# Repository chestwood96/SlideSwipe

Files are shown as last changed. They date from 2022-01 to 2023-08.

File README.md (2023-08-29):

# SlideSwipe 1.0 (magnetic probe for the voron v0.1)
## Introduction
I liked the idea of the [SideSwipe](https://github.com/oldfar-t/Side-Swipe-Magnetic-Probe) probe but didn't like that it would require either printing with the door open or losing Y travel, so I made my own take on the idea.

Taking probe             |  Stowing probe
:-------------------------:|:-------------------------:
Take  |  Stow

## Pros and cons compared to SideSwipe
| Pro | Con |
| ---- | ---- |
| + Fully integrated | - Requires new cowling (and the accompanying rebuild of everything on it) |
| + Cables well hidden | - More complex (more parts, more steps) |
| + No loss in y area with the door closed |  |
| + Bed can't hit the arm |  |
| + Hot-swappable switches (ok, fair that's a bit of a gimmick)

There is also the [option](Alternative_Mounts/FrontCowlingMount/README.md) of mounting it to the front of the cowling instead of using a new cowling if that is not an option.

## BOM
### Parts
- 1x MG90s Metal gear servo (the SG90 plastic gear ones work too but are not reccomended)
- 1x Omron(or omron size) mouse switch (I am using a kailh GM4.0 switch, but it's only marginally better than all the other switches I tested)
- 5x 6x3mm round magnets (I used the cheapest crappiest ones I could find off aliexpress, need to be at least 2.7mm thick)
- 1x 300mm servo extender cable (or make your own)
- 1x 1.5m of stranded wire with <1.2mm od (I tested 30awg silicone wire and 26awg ptfe wire)
- 2x JST-XH housing (only one housing and 2 crimping terminals if you don't want to wire to the 5pin probe port on the SKR mini E3 v2)
- 7x JST-XH female crimping terminal
- 1x (optional but reccomended) JST-PH or JST-XH 2pin male and female connector pair
- 3x 16mm piece of 4od2id PTFE tube (does not need to be the nice stuff)
- 1x 7mm piece of 4od2id PTFE tube (does not need to be the nice stuff) 
### Screws
- 7x M3x6 Socket head screw (cap head probably work too, as long as they are at least slightly attracted to magnets)
- 2x M3x8 Cap head screw
- 2x M3 nut
### Tools
- Some superglue
- Tools to crimp JST-XH (and optionally JST-PH)
- A multimeter

## Printing
All parts are designed to print in the orientation they come in and do not require supports (If you have really bad overhang performance you can add a bit of support for the probe but it should not be necessary).

Designed to print in ABS at 0.4mm outer perimeter width and 0.2mm layer height.

I recommend ironing for the following parts, the rest can be printed without:
- Arm1
- Arm2
- ProbeCarrierTop
- ProbeCarrierBottom
- RailMountTop

If you are going to do accents, I recommend printing the following parts in the accent color:
- Arm1
- Arm2
- Probe

## Build
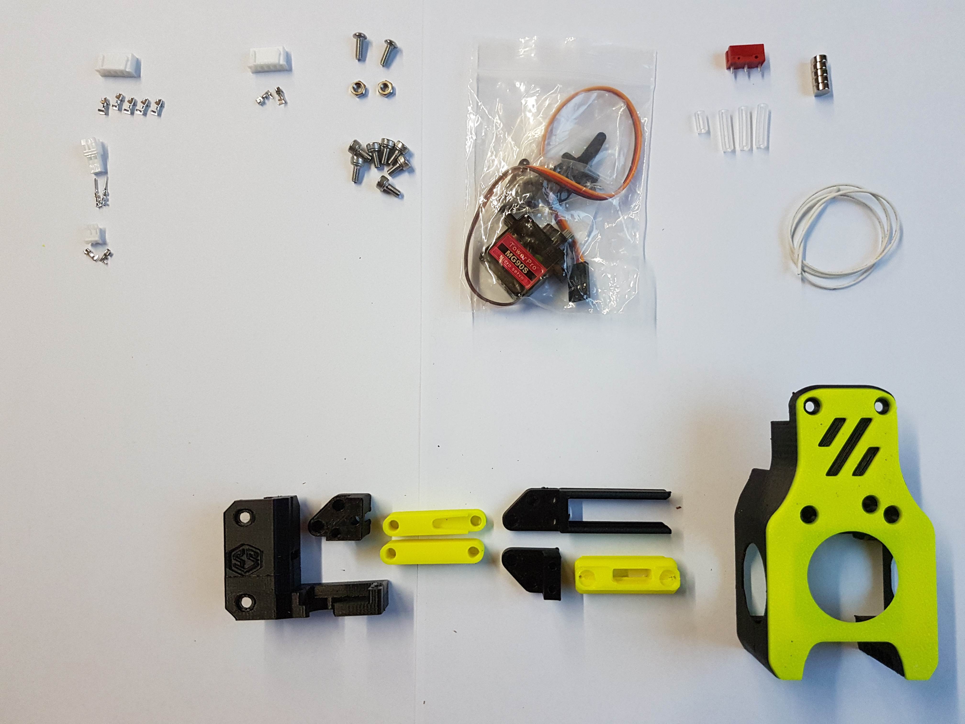
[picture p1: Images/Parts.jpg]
Parts

### Probe
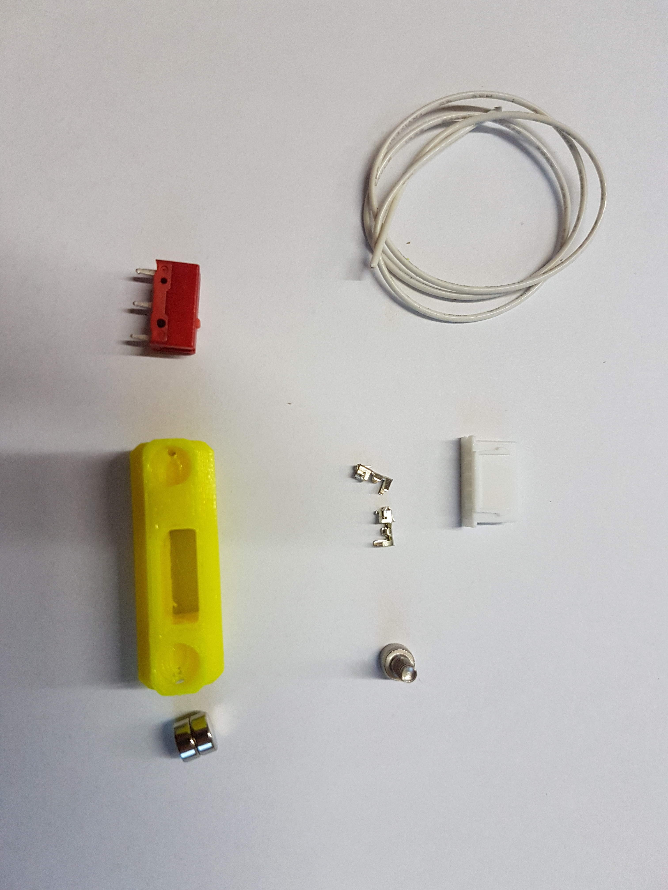
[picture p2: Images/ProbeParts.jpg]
ProbeParts


Crimp two short (about 5cm but cutting off is easier than adding...) pieces of wire and put them in the outer-most places in the JST-XH 5pin housings. I recommend testing the cripms at this point.
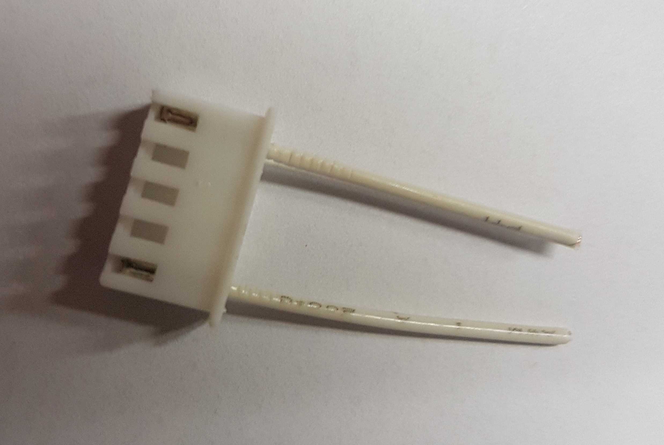
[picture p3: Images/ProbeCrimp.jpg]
ProbeCrimp


Thread the wires through the holes, then put the connector in the probe. Make sure it's the right way around. Don't put it in all the way yet.
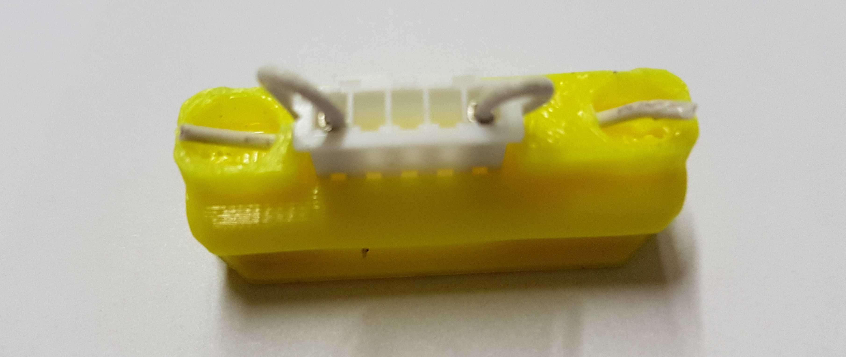
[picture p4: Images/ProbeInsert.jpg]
ProbeInsert


Add some superglue to the back of the connector and carefully push it all the way in while making sure the wires are not pinched. Make sure superglue does not get anywhere it shouldn't.
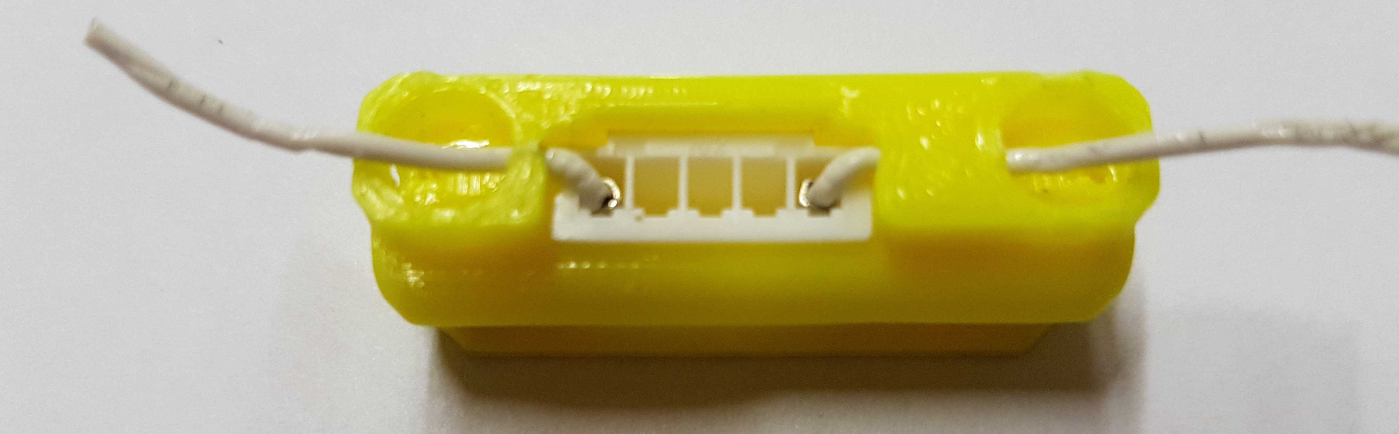
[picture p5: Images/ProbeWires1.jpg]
ProbeWires1


Shorten the wires, so they extend a little past the edge (5-10mm is fine).
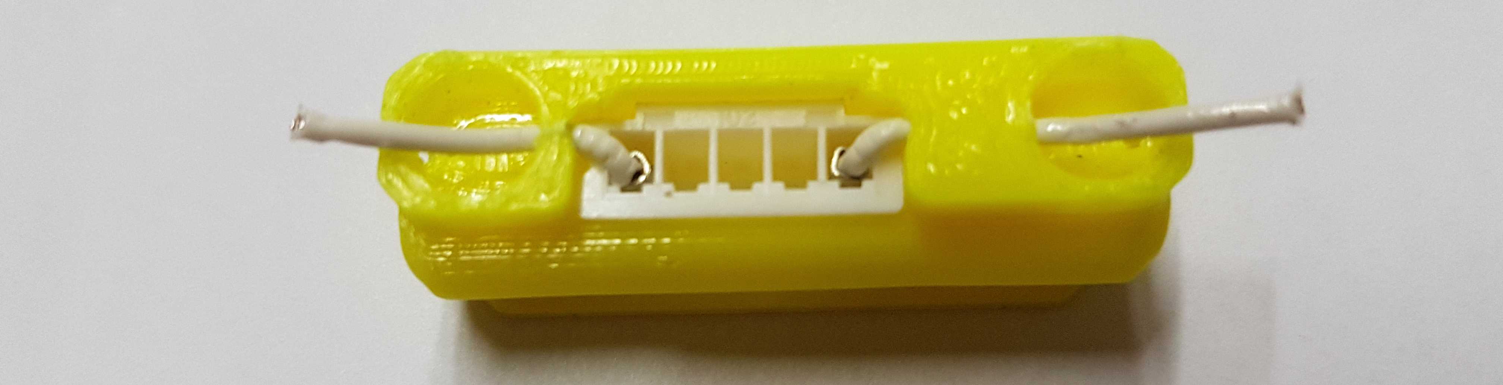
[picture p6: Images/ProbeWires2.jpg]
ProbeWires2


Strip as much of the wire as you can. You probably can't use normal wire strippers for that.
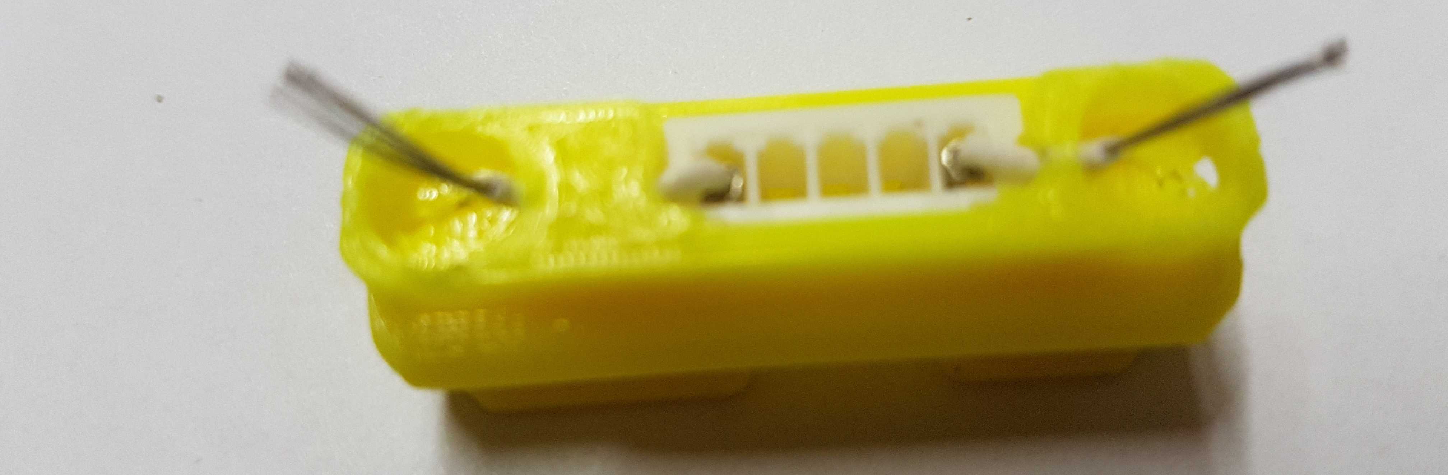
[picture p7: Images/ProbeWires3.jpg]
ProbeWires3


Put the stripped wires in the magnet holes. Make sure the unstripped parts are in the grooves, so they don't get in the way.
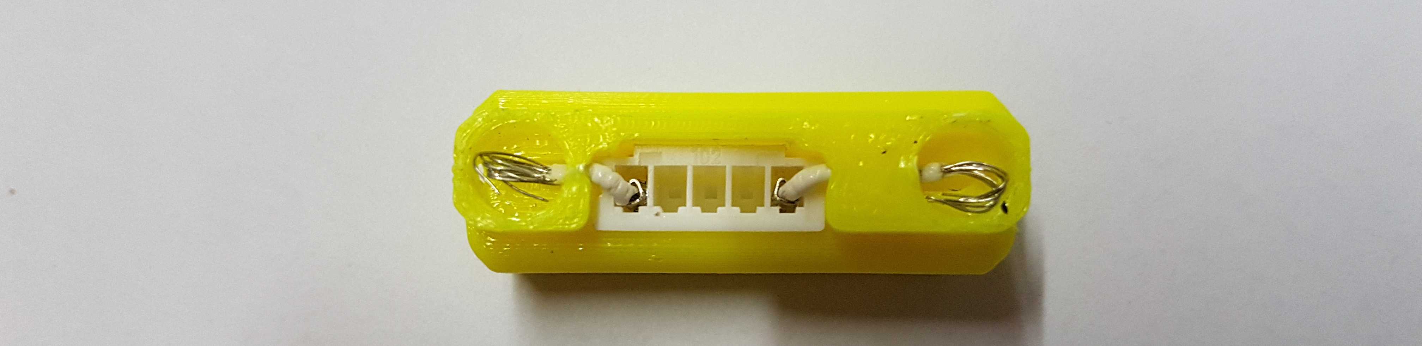
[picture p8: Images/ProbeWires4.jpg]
ProbeWires4


Add some superglue to the rim of the holes and put the magnets in the holes **with the same polarity facing up**. Make sure the glue does not get on the wires too much and there is none on the top of the magnets. Also, try to get them as parallel with each other as possible (pressing them against a flat surface while drying helps). 

Test continuity between the magnet and the jst pins.
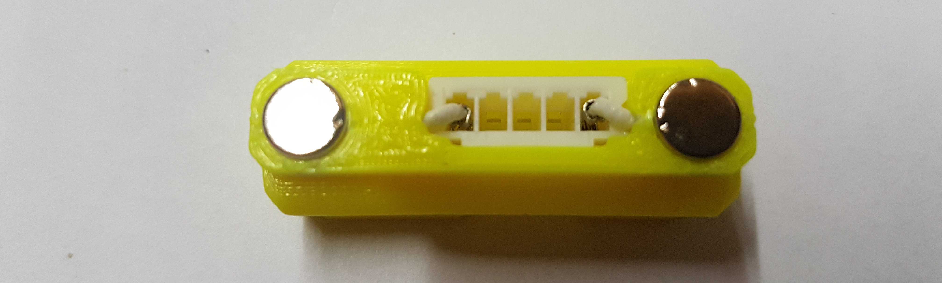
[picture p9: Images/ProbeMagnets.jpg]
ProbeMagnets


After the glue has dried insert the microswitch so the plunger is in the middle of the probe.

With the switch inserted there should be continuity between the magnets unless the switch is pressed.
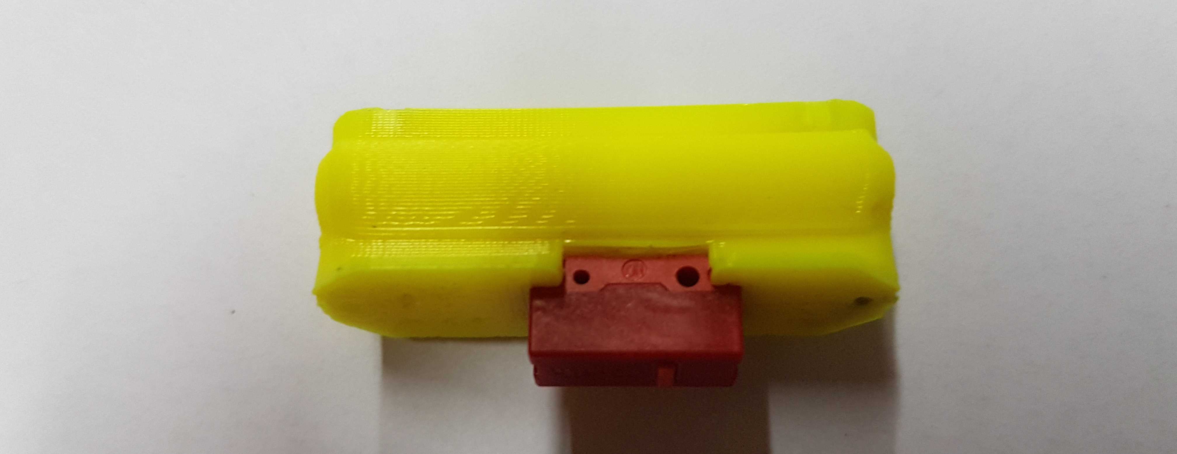
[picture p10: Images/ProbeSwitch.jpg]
ProbeSwitch


Screw on an M3x6 screw into the hole of the side of the probe. (Make sure the screw is at least somewhat attracted to a magnet)
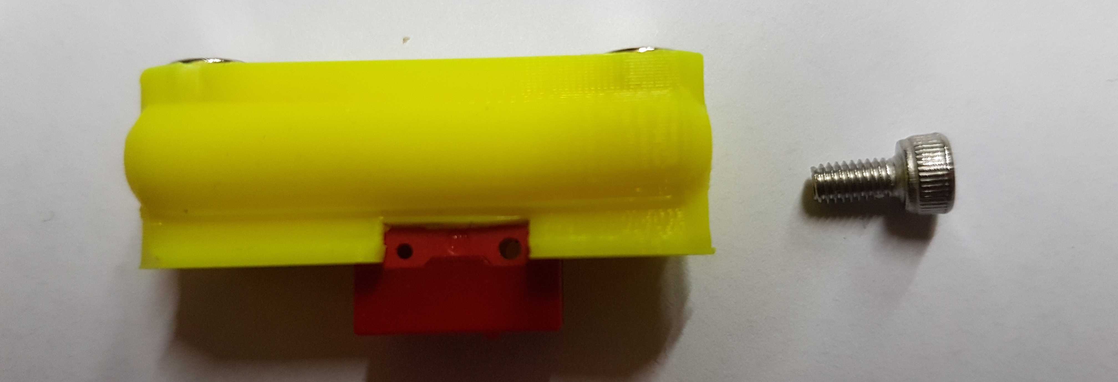
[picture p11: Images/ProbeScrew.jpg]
ProbeScrew

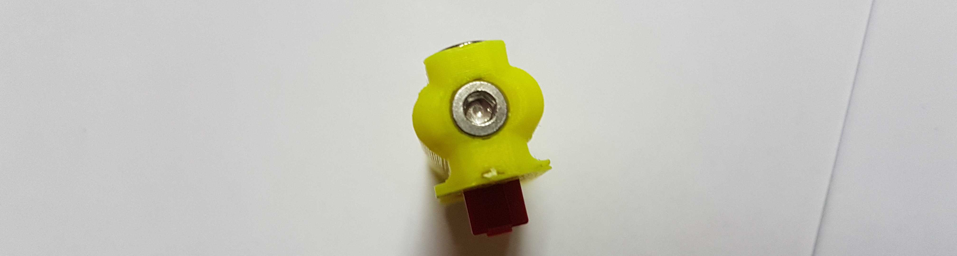
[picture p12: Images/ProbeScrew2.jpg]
ProbeScrew2


The screw is not only attracted to magnets in one direction (because of the influence from the magnet above it). Install the retention magnet in the probe carrier in the right orientation (using the probe as a tool for installing it can help). Then add some glue to the back of the magnet to hold it in place (there is a hole in the part to allow easier gluing and removal of the magnet)
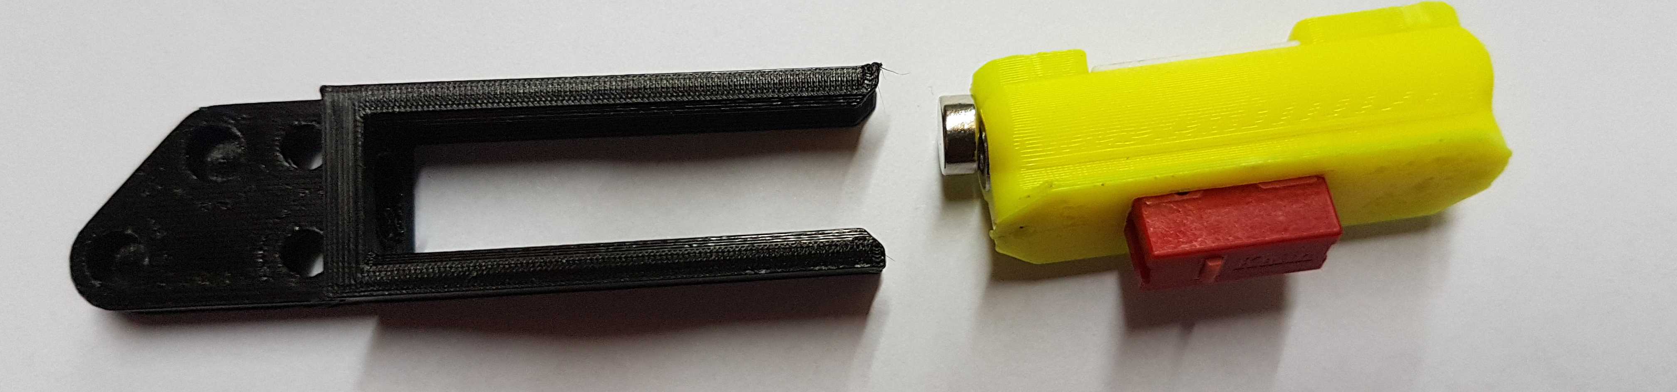
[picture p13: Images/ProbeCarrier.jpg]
ProbeCarrier

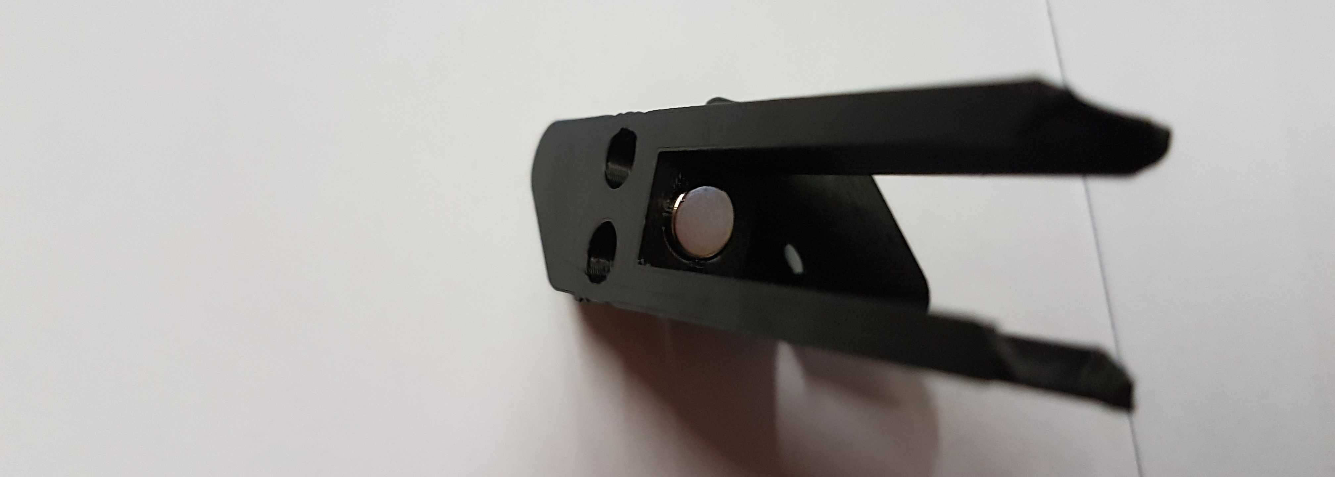
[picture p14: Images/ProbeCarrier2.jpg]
ProbeCarrier2


The probe should now stick in the carrier and not just fall out.
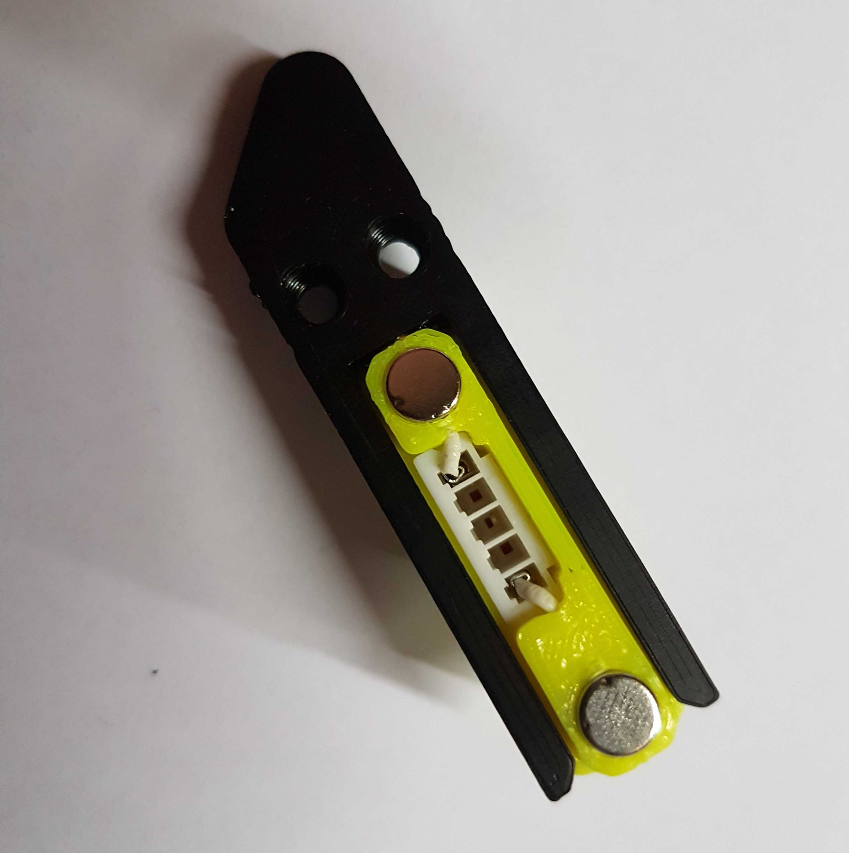
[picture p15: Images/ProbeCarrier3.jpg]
ProbeCarrier3


### Cowling
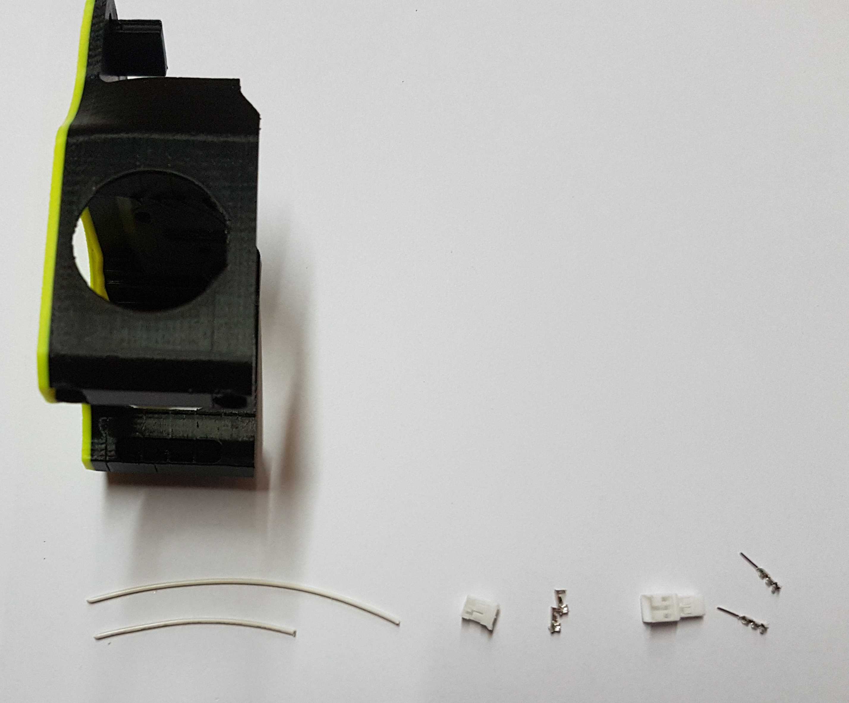
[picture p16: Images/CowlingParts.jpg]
CowlingParts


In this guide I am putting a connector (jst-ph) on the cowling for easier removal, you can use any other small enough connector or wire it directly (you just need to make the wires long enough to go through the umbilical and to your mainboard plus a little slack, so you can take the cowling of at least somewhat)

Crimp your connector to two short pieces of wire to your connector and feed them through the wire holes in the back of the cowling. Check your crimps.
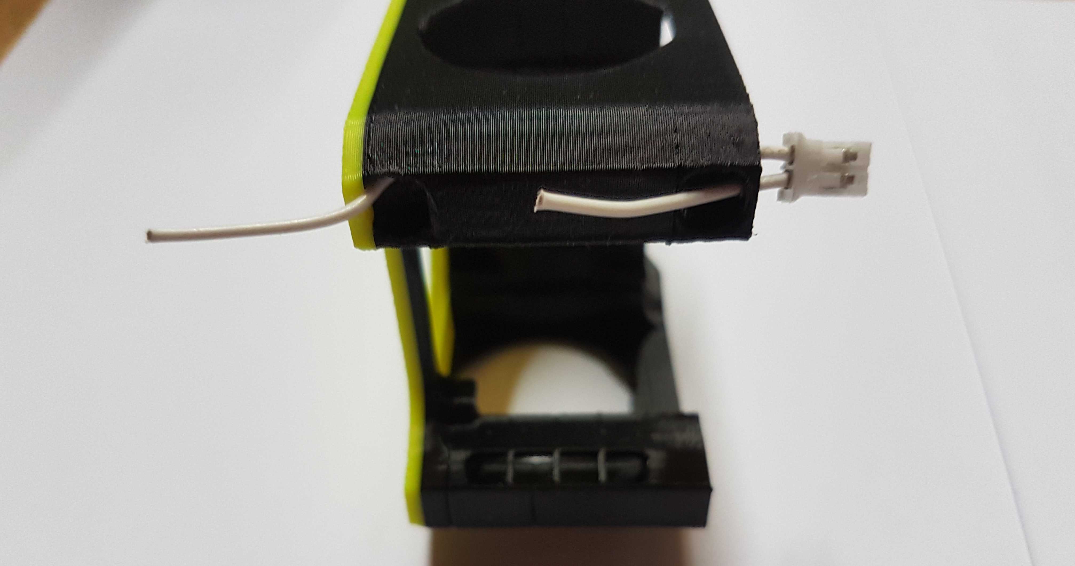
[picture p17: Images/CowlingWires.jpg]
CowlingWires


Cut them so about 3-4cm of wire are extending past the holes, then strip about 2cm off those.
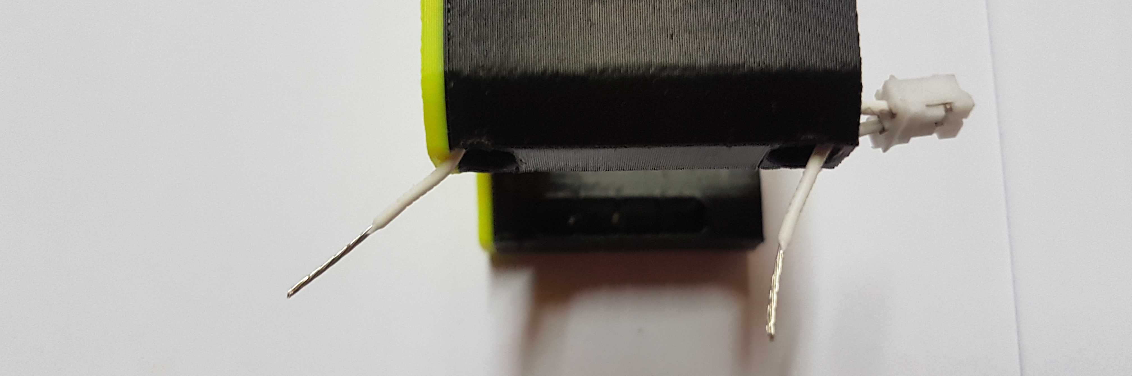
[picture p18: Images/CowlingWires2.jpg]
CowlingWires2


Pull the wires back until there is only stripped wire in the holes and curl the rest of the wire in the holes.
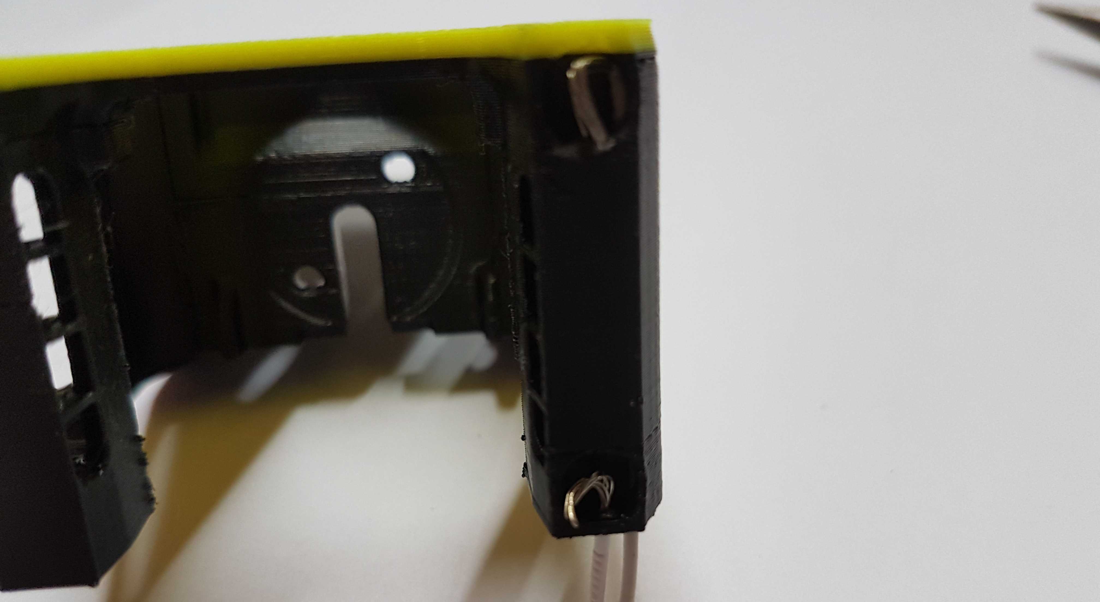
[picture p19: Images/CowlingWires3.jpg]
CowlingWires3


Put some superglue on the rims of the holes and push the magnets in the holes **in the right orientation to match the probe**. Try to get those two as parallel to each other as possible by pushing them against a flat surface.

Make sure there is no glue on the top of the magnets and check continuity between the magnets and the wires.

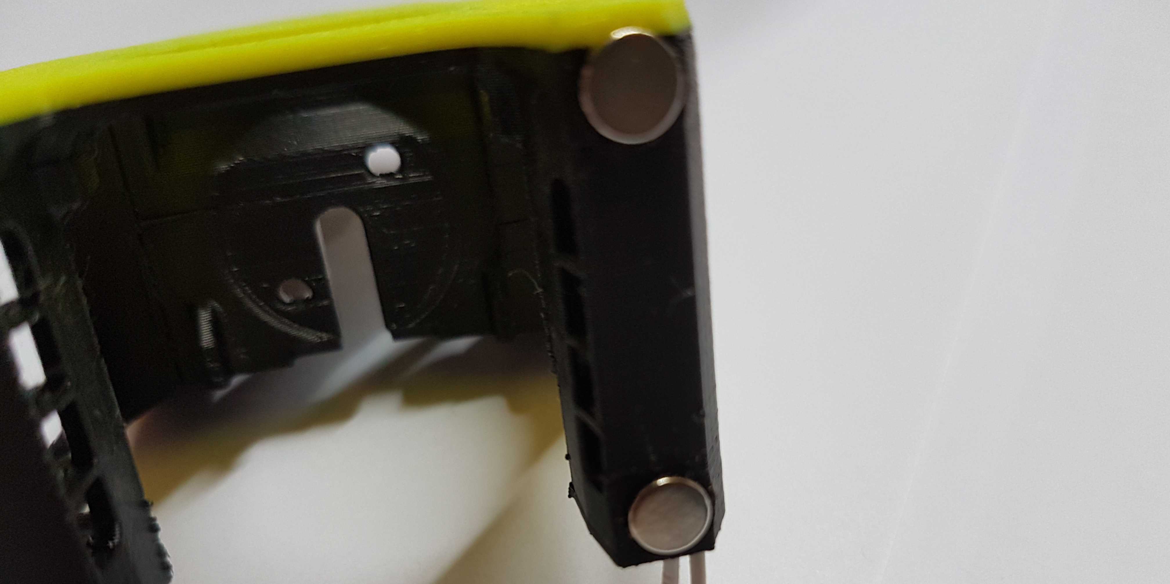
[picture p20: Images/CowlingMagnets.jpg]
CowlingMagnets


If the magnets were put in the right way the probe should stick to the cowling. Test the continuity between the wires. There should be continuity between the wires unless the switch is pressed or the probe is removed.
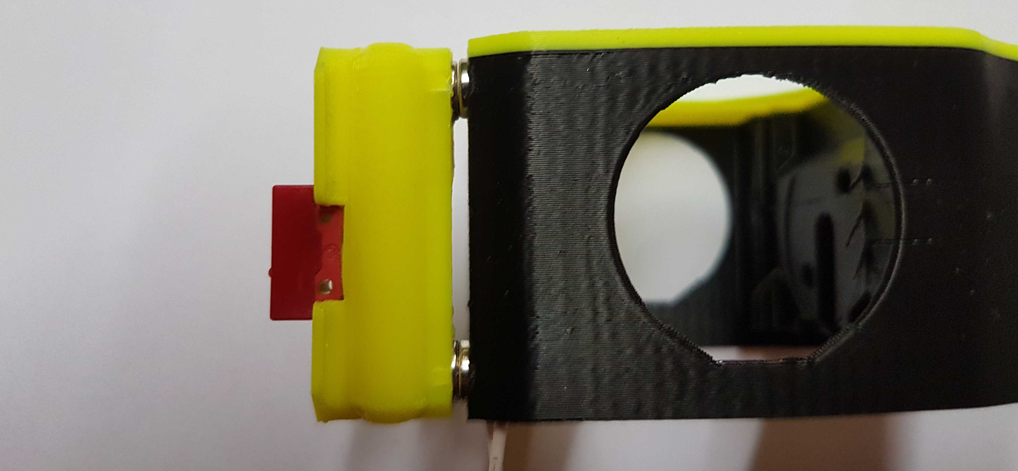
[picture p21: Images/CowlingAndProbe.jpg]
CowlingAndProbe


### Probe holder
Find the servo arm that fits the arm the best and cut off anything else on that arm if there is anything.
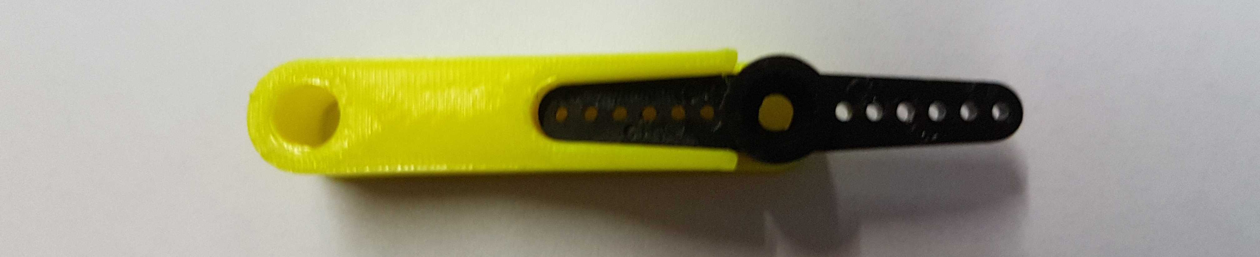
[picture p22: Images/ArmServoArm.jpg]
ArmServoArm

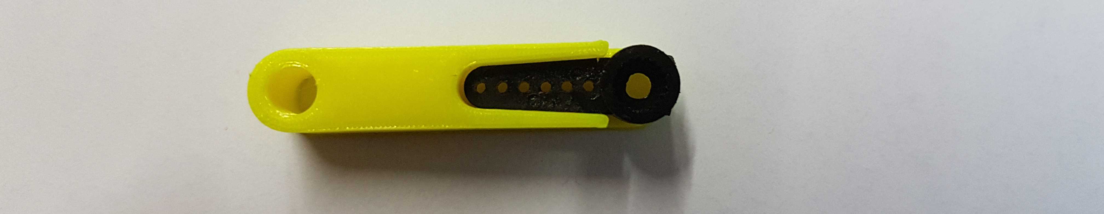
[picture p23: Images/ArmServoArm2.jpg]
ArmServoArm2


Zero the servo (and check that it has at least over 90° of travel and isn't a continuously rotating one) and install the chosen arm so it points a little over 90° when at the max point (picture is the max point).
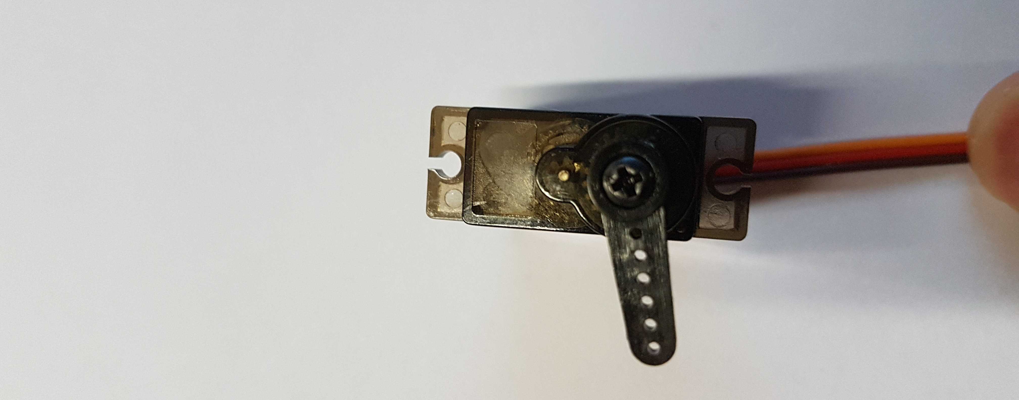
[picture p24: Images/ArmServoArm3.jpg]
ArmServoArm3


Pull the servo wire through the hole.
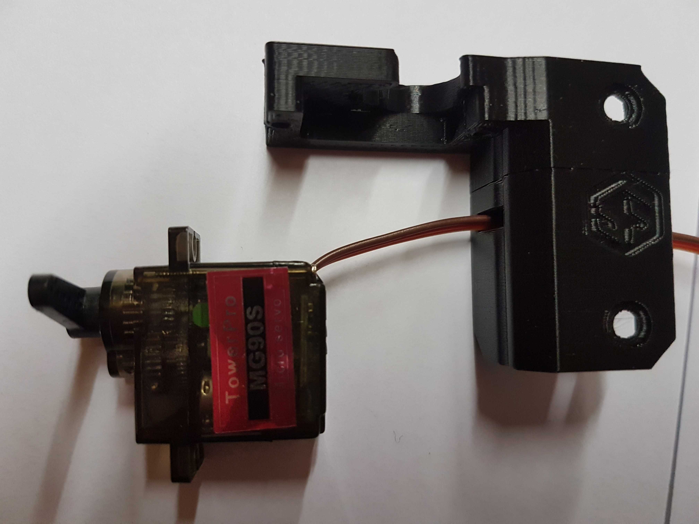
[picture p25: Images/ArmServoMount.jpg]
ArmServoMount


Insert the servo into the mount and fix it using 2 M3x6 screws
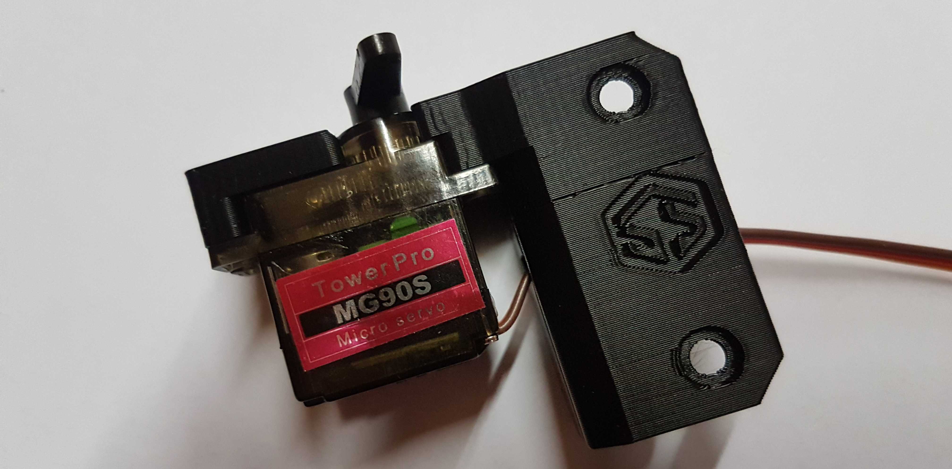
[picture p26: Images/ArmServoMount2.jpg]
ArmServoMount2

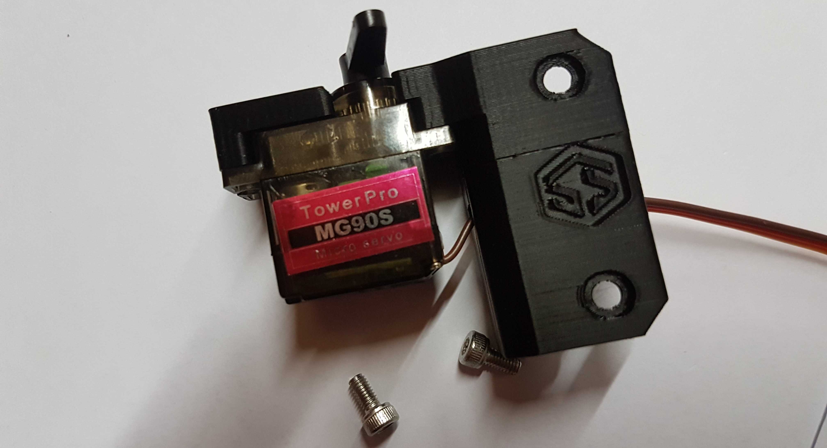
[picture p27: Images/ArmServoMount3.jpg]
ArmServoMount3

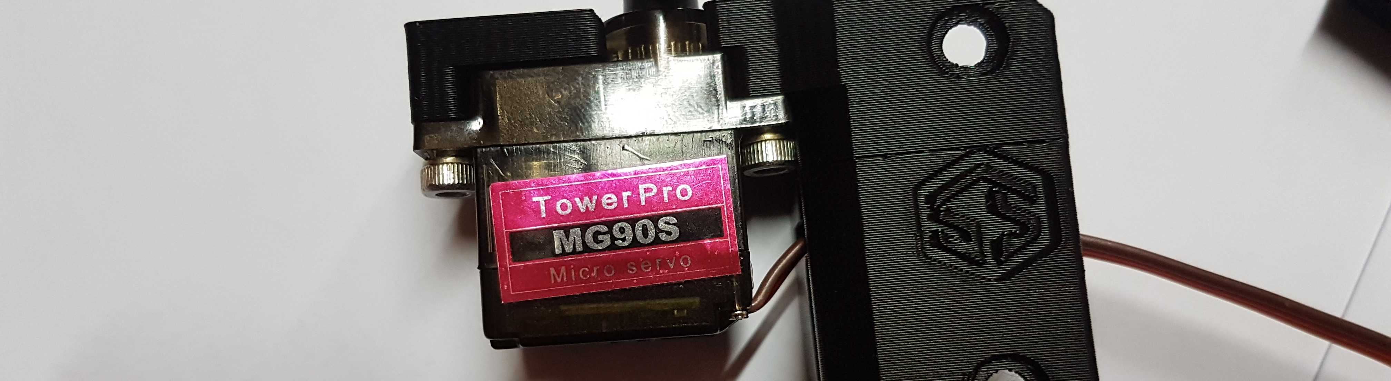
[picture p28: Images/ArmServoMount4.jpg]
ArmServoMount4


Insert the short piece of PTFE in the left hole of "RailMountTop".
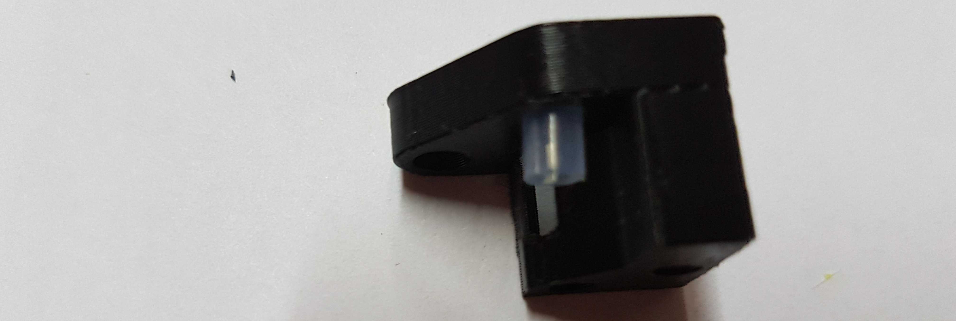
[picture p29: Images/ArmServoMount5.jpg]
ArmServoMount5


Insert one of the longer pieces of ptfe into one of the holes of "Arm2" (the solid one).
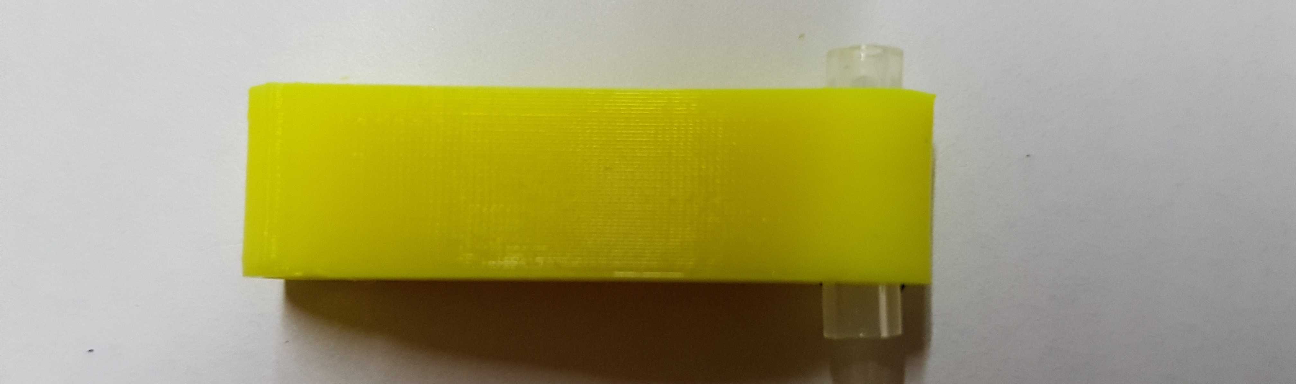
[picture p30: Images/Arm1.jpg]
Arm1


Put "Arm2" and "Arm1" onto the servo carrier like shown.
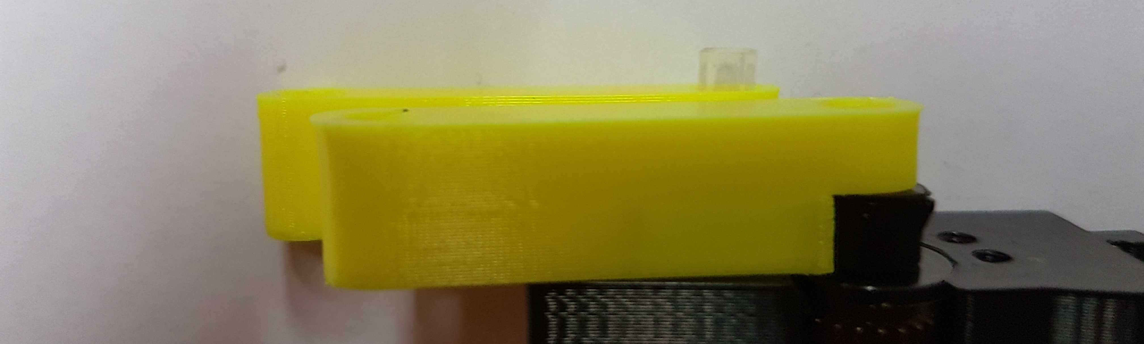
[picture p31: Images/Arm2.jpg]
Arm2


Screw "RailMountTop" onto the servo carrier using 2 M3x6 screws.
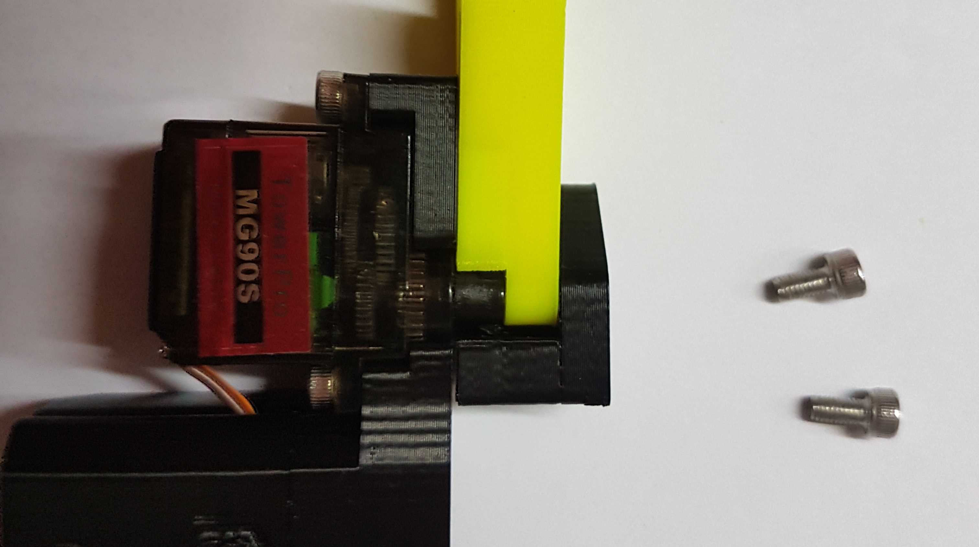
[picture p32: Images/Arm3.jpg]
Arm3


Put the other two longer pieces of ptfe into the remaining two holes in the arms.
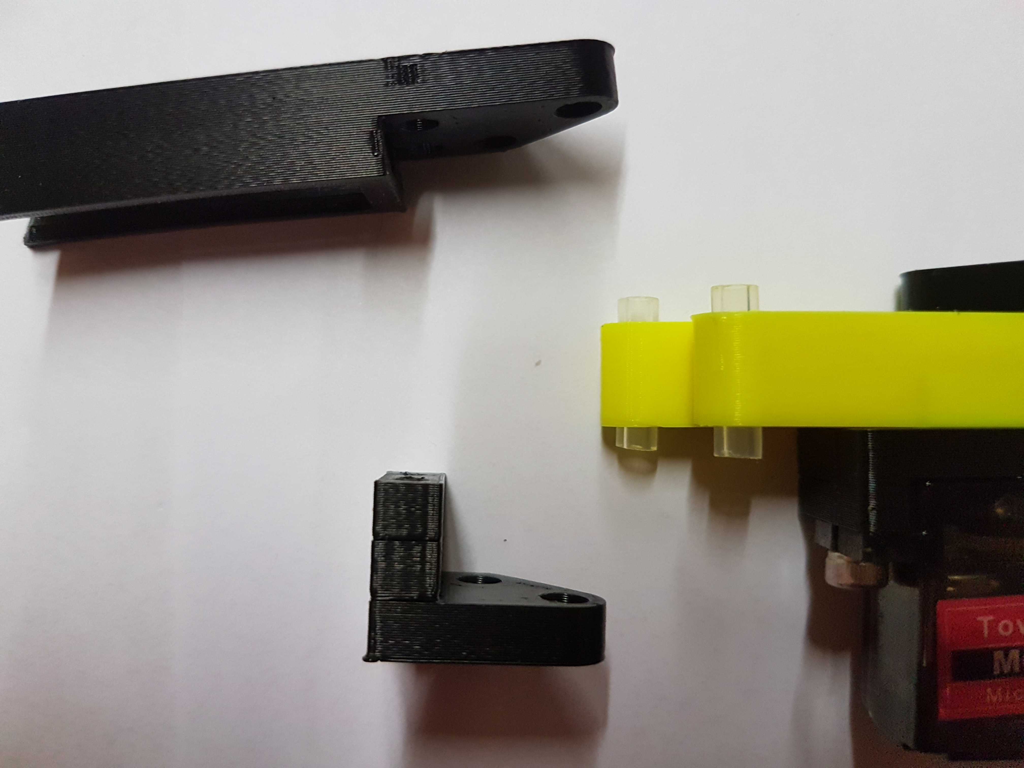
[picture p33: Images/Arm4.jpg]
Arm4


Put "ProbeCarrierTop" and "ProbeCarrierBottom" on the arms and screw them down using 2 M3x6 screws.
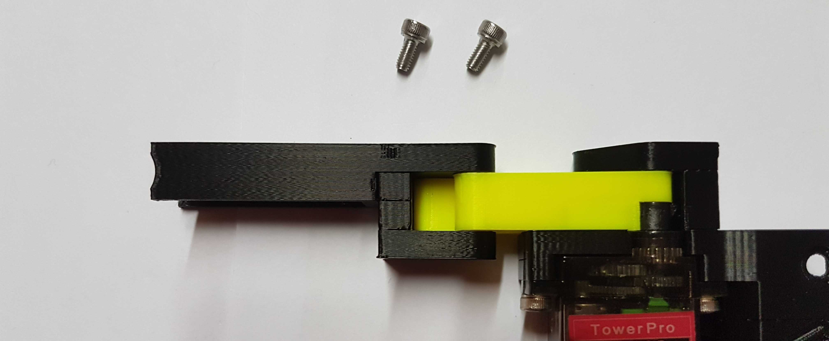
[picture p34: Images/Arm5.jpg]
Arm5

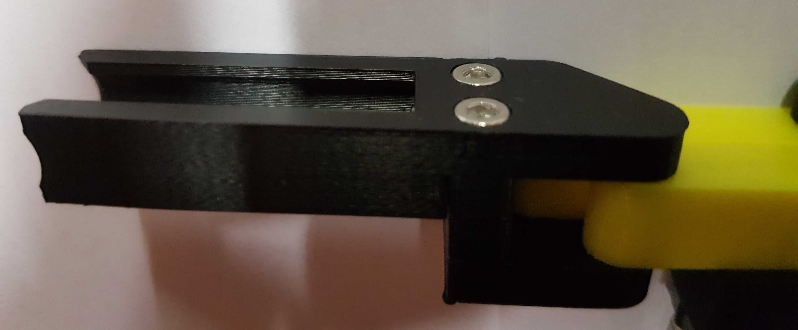
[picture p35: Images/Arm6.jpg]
Arm6


Add nuts in the pockets on the inside of the mount.
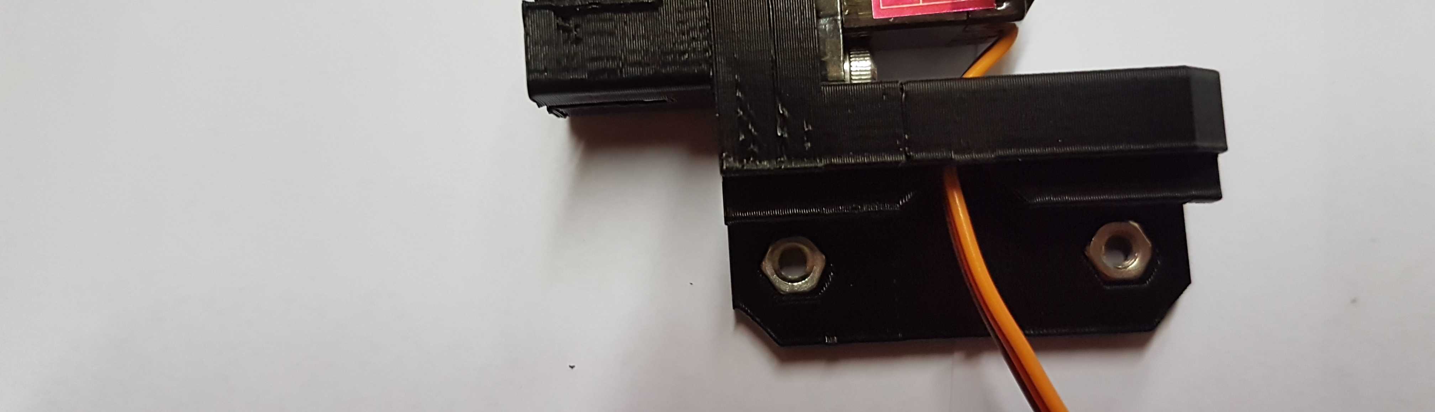
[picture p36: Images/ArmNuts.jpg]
ArmNuts


That should be the physical build done.
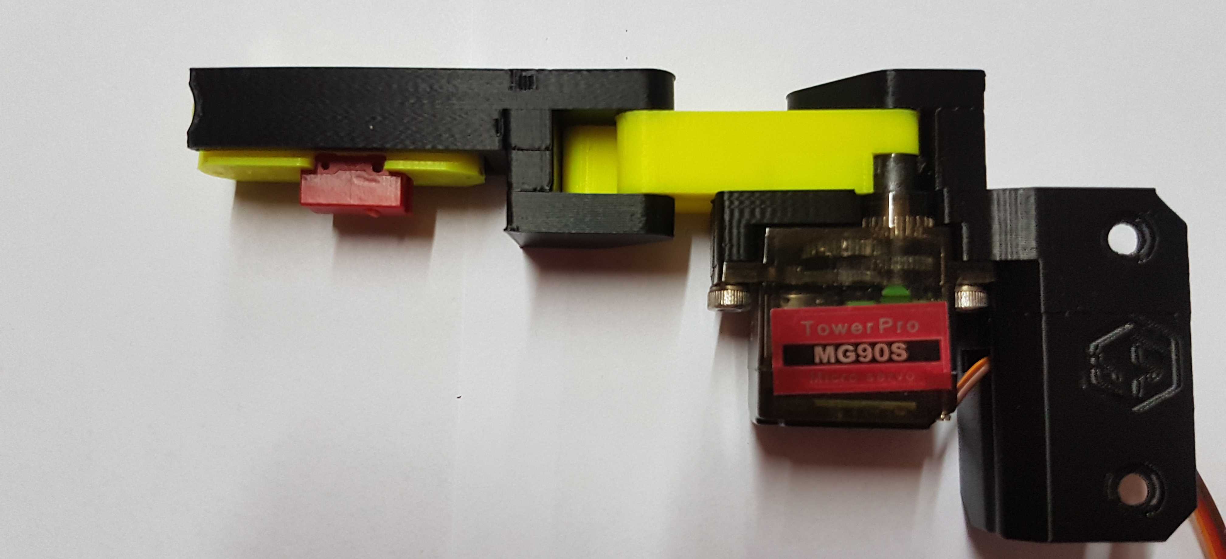
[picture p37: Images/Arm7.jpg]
Arm7


## Installation
### Installing the new cowling
The installation is the same as with the regular one, refer to the manual for that.

### Installing the probe arm
put the servo wire into the groove of the extrusion and tip the mount into it. Fix the assembly using the screws on the side.

Adjust the height to where it can grab the probe, but the arm does not hit the printhead then fix it in place.

Route the servo wire through the slot in the front extrusion upwards into the slot of the top extrusion. The stock wire should be just long enough to pass through the panel, though you'll probably have to remove the connector housing for that.

## Wiring
In this example I am hooking up to the "BL-Touch" connector of the SKR mini e3 v2.0

If you are fancy you can crimp that onto a 5 pin jst-xh plug, otherwise you can just plug it straight into the header.

Here is a crude diagram of how this could be wired up. If you wired it differently you'll need to pay special attention during the klipper setup.
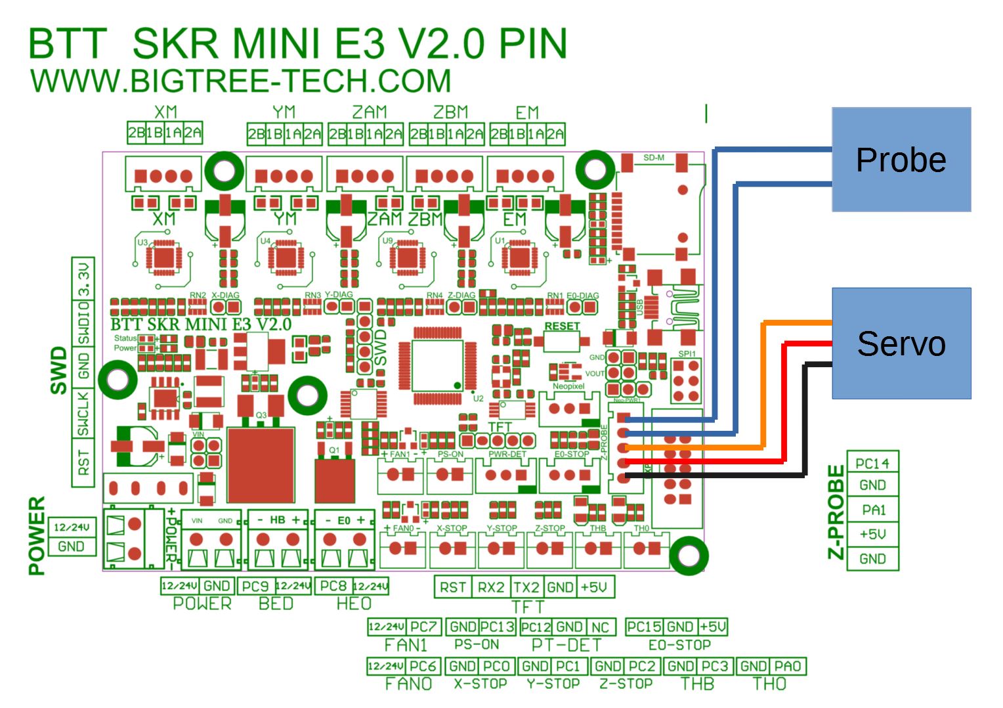
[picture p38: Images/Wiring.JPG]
Wiring


## Klipper setup

Put this in your klipper config. If you wired it differently, adjust the pins for the probe and the servo
```
[homing_override]
axes: z
gcode:
    SET_KINEMATIC_POSITION Z=0
    G1 Z5
    G28 X Y
    Query_Probe
    SS_CONDITIONAL_TAKE_PROBE
    G1 X40 Y110
    G28 Z
    G91
    G1 Z1
    G90

[probe]
pin: ^PC14
x_offset: 20
y_offset: 0
z_offset: 10
speed: 20.0
samples: 2
sample_retract_dist: 5.0
lift_speed: 30.0
samples_tolerance: 0.01
samples_tolerance_retries: 15
deactivate_on_each_sample: 0

[bed_mesh]
speed: 200
horizontal_move_z: 25
mesh_min: 25,25
mesh_max: 95, 95
probe_count: 3,3
algorithm: bicubic

[servo probeServo]
pin: PA1
minimum_pulse_width: 0.000544

[gcode_macro SS_PICKUP_POS]
variable_x: 115
variable_y: 50
variable_z: 30
gcode:
  M118 pickup pos X:{printer["gcode_macro SS_PICKUP_POS"].x} Y:{printer["gcode_macro SS_PICKUP_POS"].y} Z:{printer["gcode_macro SS_PICKUP_POS"].z}

[gcode_macro SS_DEPLOY]
gcode:
    SET_SERVO SERVO=probeServo ANGLE=160
    G4 P500 # wait for deploy
    #SET_SERVO SERVO=probeServo WIDTH=0 # OFF
    
[gcode_macro SS_RETRACT]
gcode:
    SET_SERVO SERVO=probeServo ANGLE=20
    G4 P500 # wait for retract
    SET_SERVO SERVO=probeServo WIDTH=0 # OFF

[gcode_macro SS_TAKE_PROBE]
gcode:
    G1 Z{printer["gcode_macro SS_PICKUP_POS"].z} F5000
    G1 X{printer["gcode_macro SS_PICKUP_POS"].x - 20} Y{printer["gcode_macro SS_PICKUP_POS"].y} F5000
    SS_DEPLOY
    G1 X{printer["gcode_macro SS_PICKUP_POS"].x}
    G1 Y{printer["gcode_macro SS_PICKUP_POS"].y + 50}
    G1 X{printer["gcode_macro SS_PICKUP_POS"].x - 20}
    SS_RETRACT

[gcode_macro SS_STOW_PROBE]
gcode:
    G1 Z{printer["gcode_macro SS_PICKUP_POS"].z} F5000
    G1 X{printer["gcode_macro SS_PICKUP_POS"].x - 20} Y{printer["gcode_macro SS_PICKUP_POS"].y + 50} F5000
    SS_DEPLOY
    G1 X{printer["gcode_macro SS_PICKUP_POS"].x}
    G1 Y{printer["gcode_macro SS_PICKUP_POS"].y} F2000
    G1 X{printer["gcode_macro SS_PICKUP_POS"].x - 20} F5000
    SS_RETRACT

[gcode_macro SS_CONDITIONAL_TAKE_PROBE]
gcode:
    {% set P = printer.probe.last_query %}
    {% if P %}
        SS_TAKE_PROBE
    {% endif %}

[gcode_macro SS_CONDITIONAL_STOW_PROBE]
gcode:
    {% set P = printer.probe.last_query %}
    {% if not P %}
        SS_STOW_PROBE
    {% endif %}

[gcode_macro G29]
gcode:
    G91
    G1 Z1
    G90
    Query_Probe
    SS_CONDITIONAL_TAKE_PROBE
    BED_MESH_CALIBRATE
    SS_STOW_PROBE

[force_move]
enable_force_move: True

[respond]
```

and replace your z endstop with the probe:
```
endstop_pin: probe:z_virtual_endstop
```

Also add the following to your print start (either in klipper or in your slicer) to make sure it won't try to print with the probe attached (the query_probe first is important):
```
    Query_Probe
    SS_CONDITIONAL_STOW_PROBE
```

After the calibration you should be able to use the G29 macro to mesh level your bed.

### Calibrating the servo angles
Using the servo command, find good values where the servo reliably hits the deployed and stowed position. The mechanism mechanically limits the travel. Having the servo try to push against it the whole time isn't great for it, so try to find some values that don't go way over the limits.

Once you have found the right values, update the "SS_DEPLOY" and "SS_RETRACT" macros with your new values.

### Calibrating the pickup position
This should already be somewhat acurate but if it isn't find the pickup position and update the "SS_PICKUP_POS" macro accordingly.

## First tests
### Check the probe and config
Let's see if klipper can see the probe. The "QUERY_PROBE" command is our friend here.

With the probe attached (by hand for now) it should return "open". With the button pressed it should return "triggered" and with the probe removed it should also return "triggered". If this is not true don't proceed, and go check your wiring and config.

If that worked out put the probe in the probe carrier and do a test run. The homing override uses the probe so all we'll have to do to see if it works is run `G28`.

It should now home x and y, then pick up the probe and probe for Z. Be ready to cut power if something weird happens.

To make sure everything has settled I like to do a couple hundred probes before I do stuff like calibrating the Z-offset.

```
PROBE_ACCURACY samples=100
```

## Calibrate Z-Offset and start printing
Use your favourite method of calibrating the z-offet and start printing.

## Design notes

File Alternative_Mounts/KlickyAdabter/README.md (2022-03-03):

# Front Cowling Mount
Thanks to Jlas1 for making this.

This is an adapter that allows using SlideSwipe on cowlings meant for klicky like the regular klicky cowling or the one for the LGX Lite.

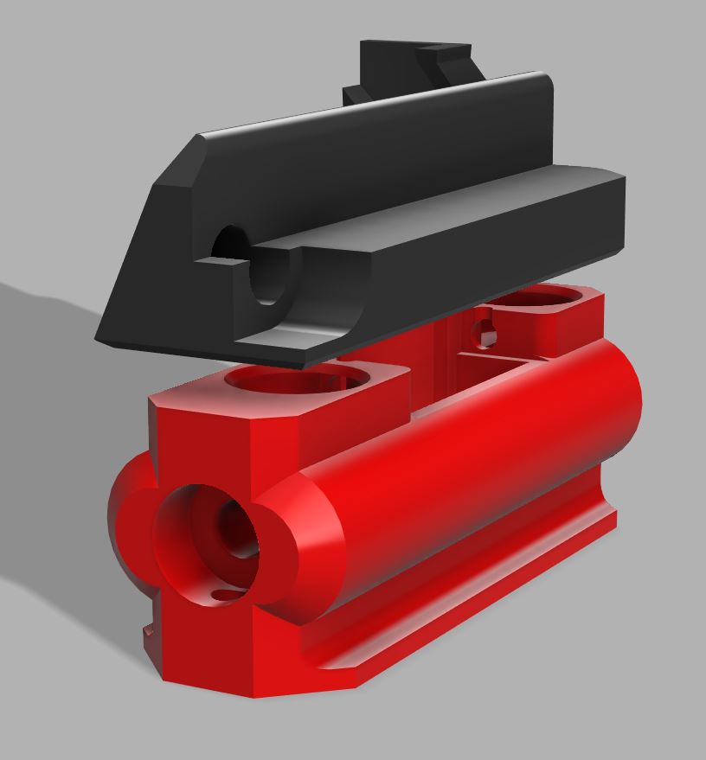
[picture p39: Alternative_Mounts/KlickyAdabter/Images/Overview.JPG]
Action


## Pros and cons compared to integrated mount
| Pro | Con |
| ---- | ---- |
| + Allows keeping the same Cowling (if you allready use one of the compatible ones) | - Probe is further away from the nozzle (can probe less of the bed) |
| + Allows switching between Klicky and Slideswipe | - Uses a slightly different probe that is not compatible with the other mounting options |

## BOM (Differences only)
### Screws
- 1x M3x6 BHSC screw

## Build
The build process is the same as normal, just substitute the cowling with the "Slideswipe_KlickyAdapter_mount" and the probe with "Slideswipe_KlickyAdapter_probe"

## Klipper Setup
The klipper setup is also almost the same, however we need a few changes, **do not try probing before this step**

## Pickup position
Move the X of the pickup position 8mm to the left, to do this change this part of the "SS_PICKUP_POS" macro from:
```
[gcode_macro SS_PICKUP_POS]
variable_x: 115
...
```
to:
```
[gcode_macro SS_PICKUP_POS]
variable_x: 107
...
```

## Probe offset
Increase the X-offset of the probe by 8mm (to 28mm):
```
[probe]
pin: ^PC14
x_offset: 28
...
```

## Change Mesh Leveling coordinates
Replace the whole "[bed_mesh]" section with this:
```
[bed_mesh]
speed: 200
horizontal_move_z: 25
mesh_min: 32,32
mesh_max: 88, 88
probe_count: 3,3
algorithm: bicubic
```

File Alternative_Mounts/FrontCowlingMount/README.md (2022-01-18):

# Front Cowling Mount
Thanks to Jlas1 for making this.

The Front cowling mount allows using SlideSwipe without printing and installing a new cowling.

Action

## Pros and cons compared to integrated mount
| Pro | Con |
| ---- | ---- |
| + No cowling rebuild required | - Probe is further away from the nozzle (can probe less of the bed) |
|  | - Floppier and more fragile |
|  | - Less aesthetically pleasing

## BOM (Differences only)
### Screws
- 2x M3x40 Cap head screw

## Build
The build process is the same as normal, just substitute the cowling with the "FrontCowlingMount"

## Klipper Setup
The klipper setup is also almost the same, however we need a few changes, **do not try probing before this step**

## Pickup position
Move the X of the pickup position 8mm to the left, to do this change this part of the "SS_PICKUP_POS" macro from:
```
[gcode_macro SS_PICKUP_POS]
variable_x: 115
...
```
to:
```
[gcode_macro SS_PICKUP_POS]
variable_x: 107
...
```

## Probe offset
Increase the X-offset of the probe by 8mm (to 28mm):
```
[probe]
pin: ^PC14
x_offset: 28
...
```

## Change Mesh Leveling coordinates
Replace the whole "[bed_mesh]" section with this:
```
[bed_mesh]
speed: 200
horizontal_move_z: 25
mesh_min: 32,32
mesh_max: 88, 88
probe_count: 3,3
algorithm: bicubic
```

# That's it
I still recomend moving to the integrated mount next time you redo the cowling.

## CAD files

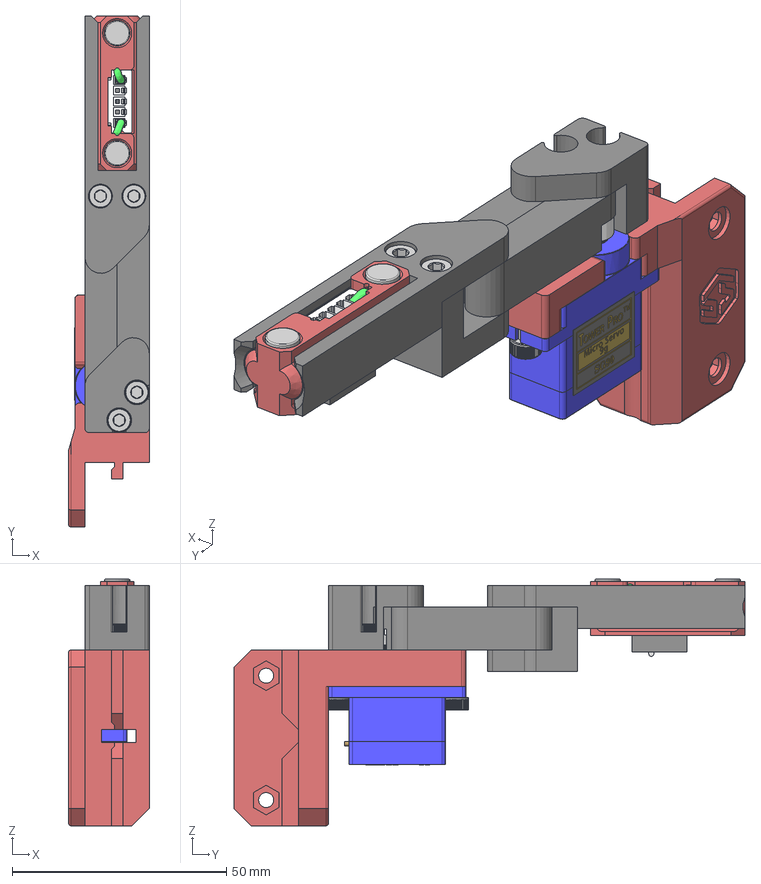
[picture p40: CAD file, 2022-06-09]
STEP/SlideSwipe_Assembly.step
18.8 x 119.2 x 57.5 mm
Arm1
Arm2
6x3 Magnet x 3
91290A111_NO THREADS_Alloy Steel Socket Head Screw x 7
Wire2
Wire1
JST-XH 5-Pin (1)
Omron_D2F_F-1
ProbeCarrierBottom
ProbeCarrierTop
16mm 4x2 PTFE Tube x 3
RailMountSide
RailMountTop
7mm 4x2 PTFE Tube
SG90 - Micro Servo 9g - Tower Pro.1_Pea
SG90 - Micro Servo 9g - Tower Pro.2_Pea

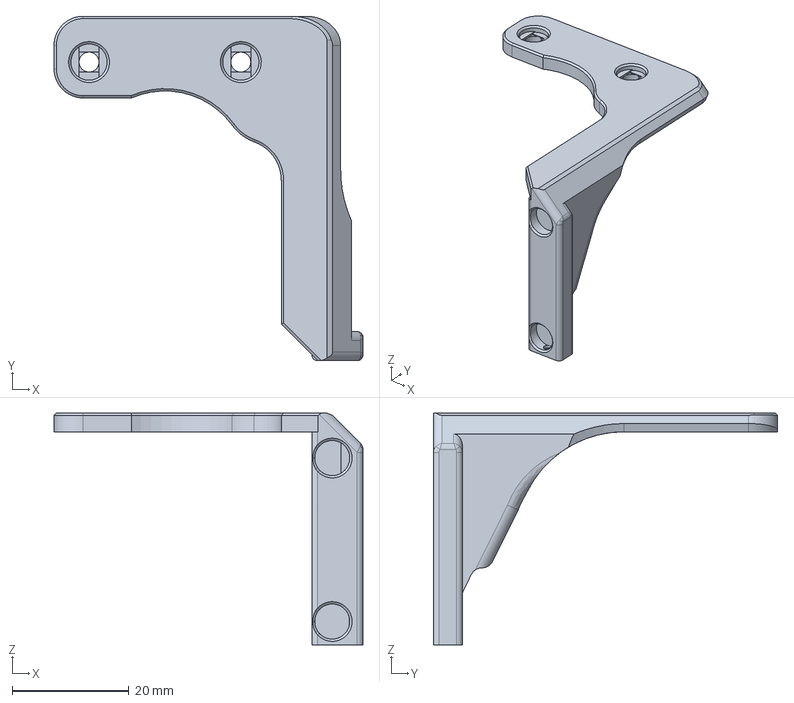
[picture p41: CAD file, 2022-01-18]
Alternative_Mounts/FrontCowlingMount/STEP/SlideSwipe_FrontCowlingMount.step
52.9 x 59.0 x 39.7 mm

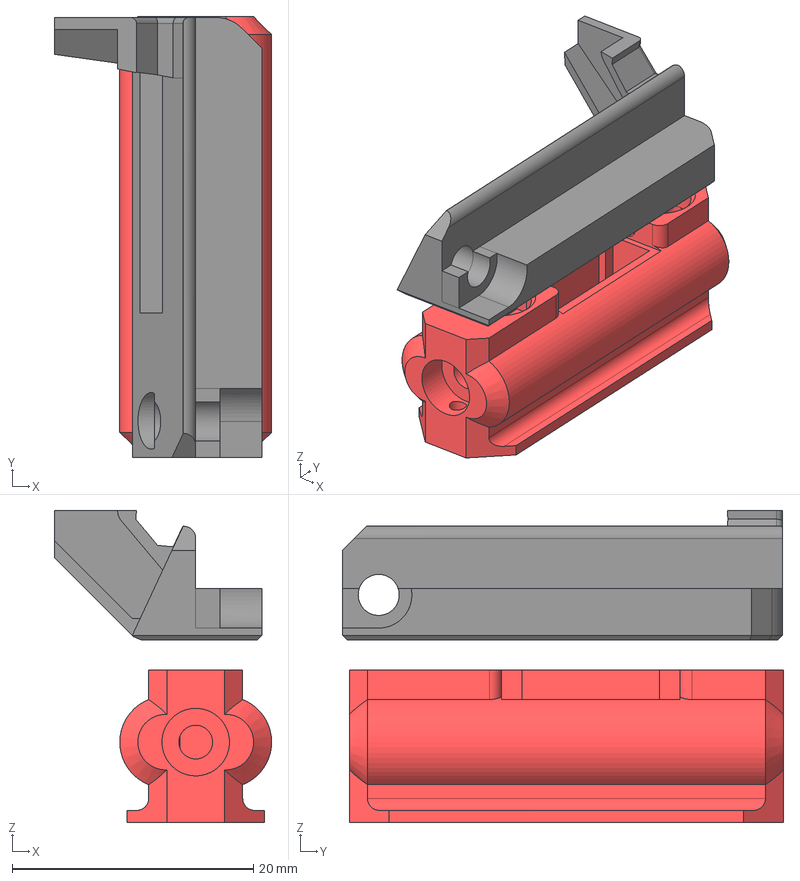
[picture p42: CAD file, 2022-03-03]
Alternative_Mounts/KlickyAdabter/STEP/SlideSwipe_KlickyAdapter.step
18.0 x 36.6 x 25.9 mm
V0.1 Slideswipe integrated mount
Slideswipe integrated probe

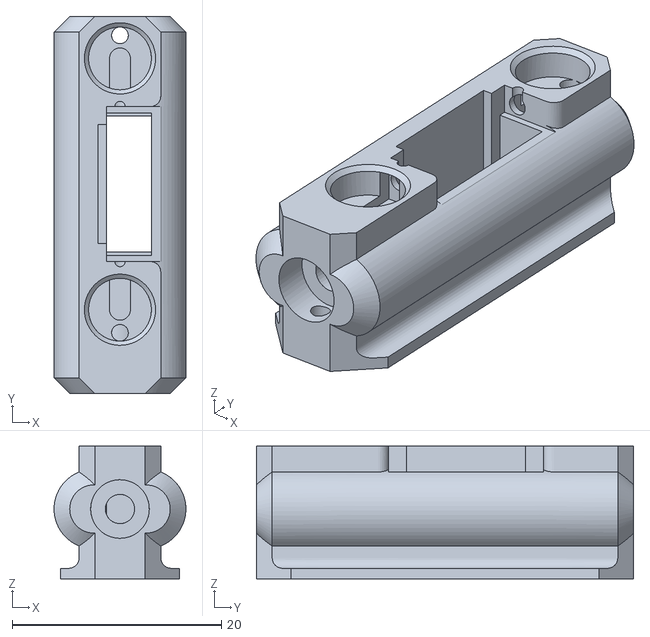
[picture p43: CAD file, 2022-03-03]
Alternative_Mounts/KlickyAdabter/STL/Slideswipe_KlickyAdapter_probe.stl
12.6 x 36.0 x 12.7

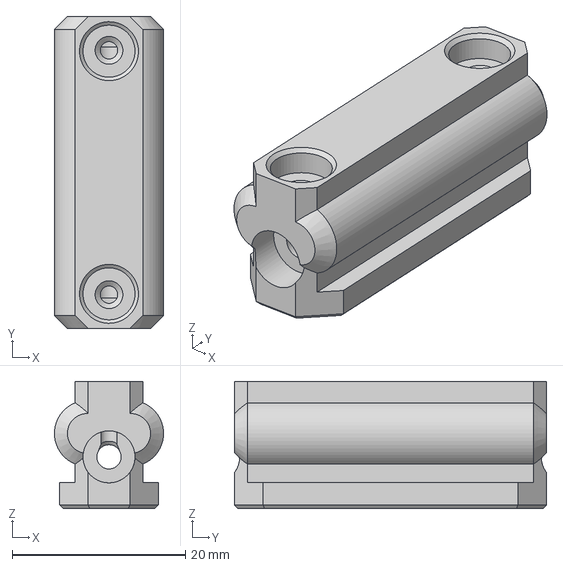
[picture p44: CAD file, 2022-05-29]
Experimental/UnklickySlideSwipe(better name pending)/STEP/ProbeLoose.step
12.6 x 36.0 x 14.7 mm

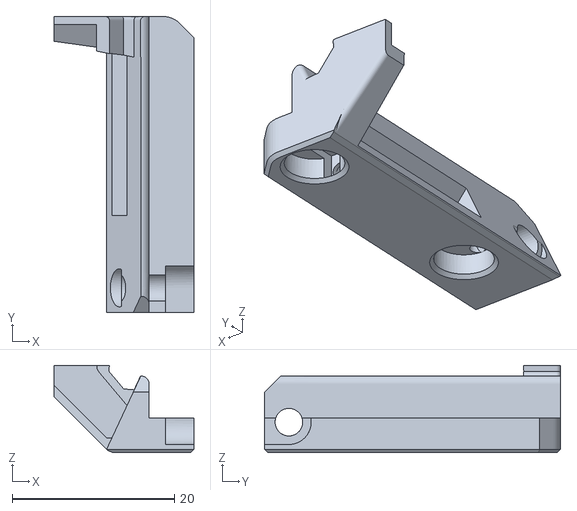
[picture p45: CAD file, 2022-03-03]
Alternative_Mounts/KlickyAdabter/STL/Slideswipe_KlickyAdapter_mount.stl
17.2 x 36.5 x 10.7

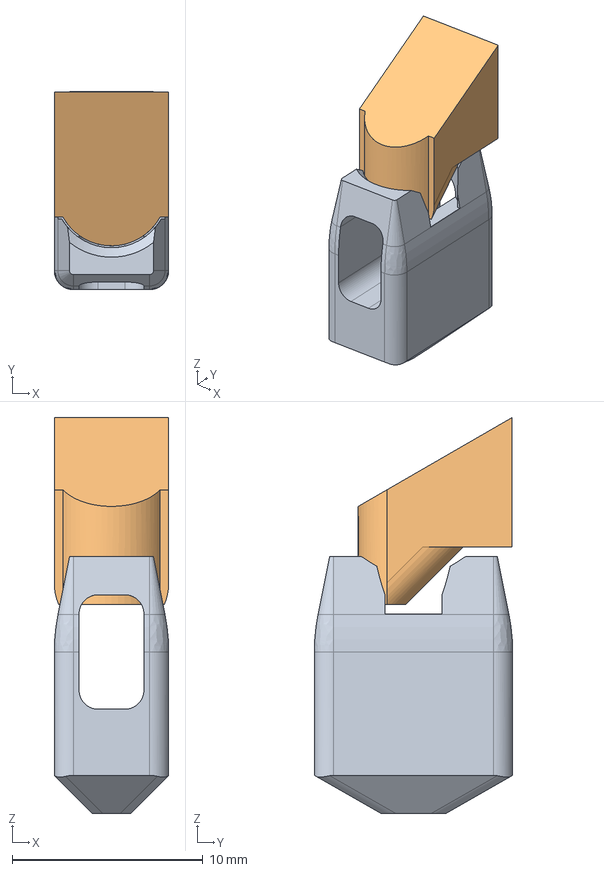
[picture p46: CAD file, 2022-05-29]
Experimental/UnklickySlideSwipe(better name pending)/STEP/PlungerSideways.step
6.00 x 10.4 x 20.8 mm

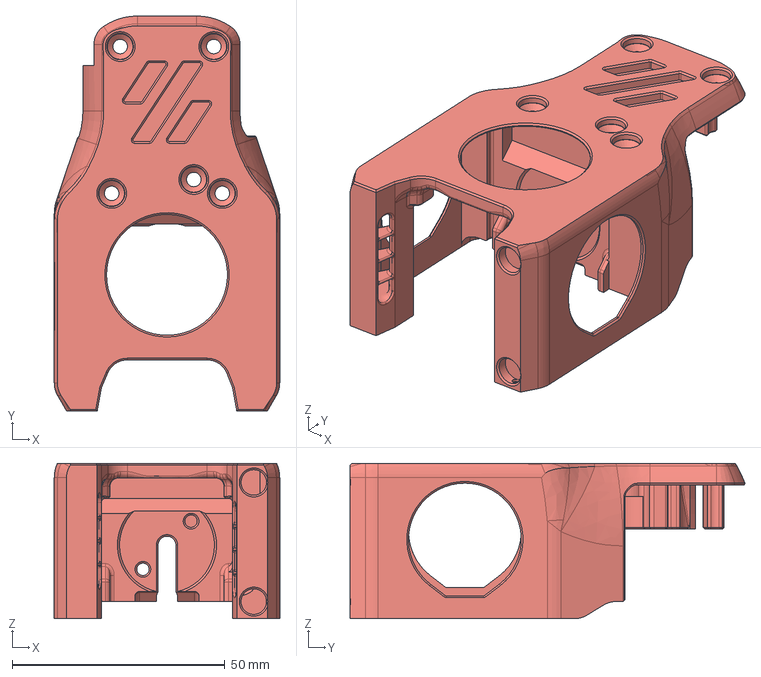
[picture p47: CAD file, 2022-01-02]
STEP/Cowling_Dragon_SlideSwipe.step
53.0 x 92.8 x 36.5 mm

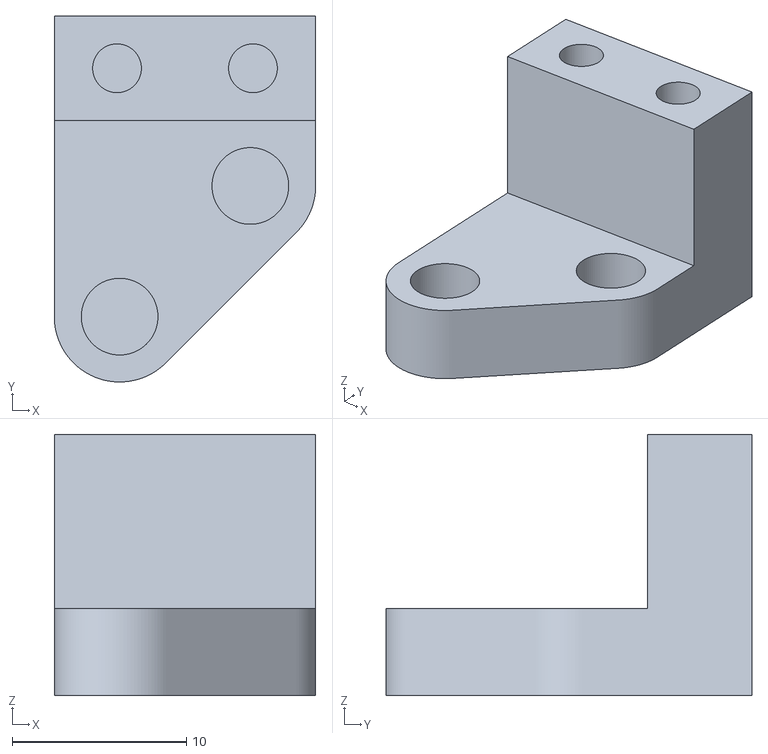
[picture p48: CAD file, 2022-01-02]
STL/ProbeCarrierBottom.stl
15.0 x 21.0 x 15.0

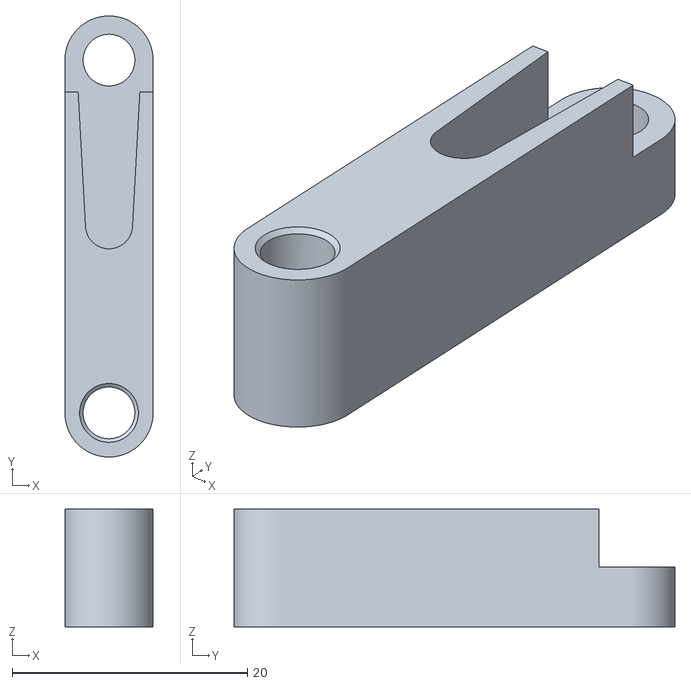
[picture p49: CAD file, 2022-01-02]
STL/Arm1.stl
7.50 x 37.5 x 10.0

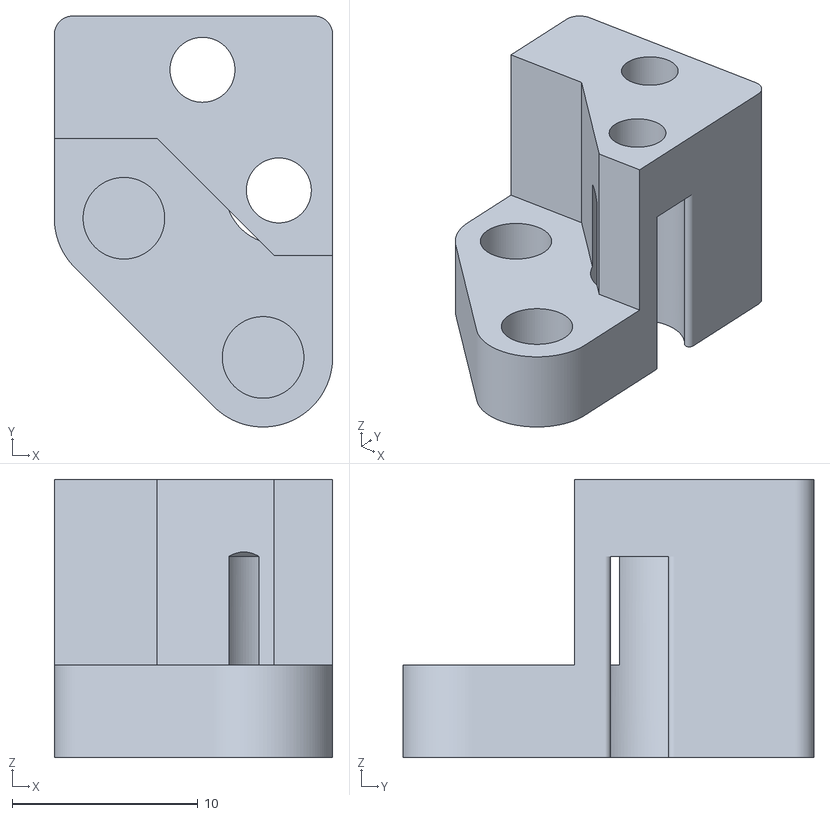
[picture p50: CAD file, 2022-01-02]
STL/RailMountTop.stl
15.0 x 22.1 x 15.0

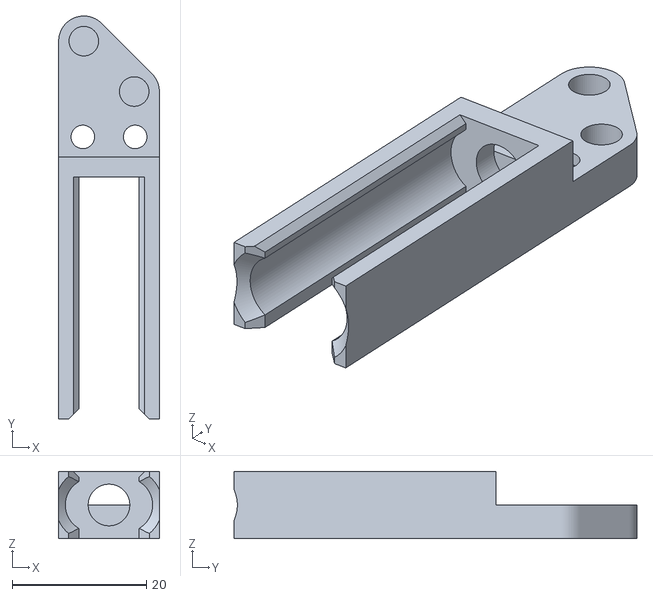
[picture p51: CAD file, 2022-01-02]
STL/ProbeCarrierTop.stl
15.0 x 60.0 x 10.0

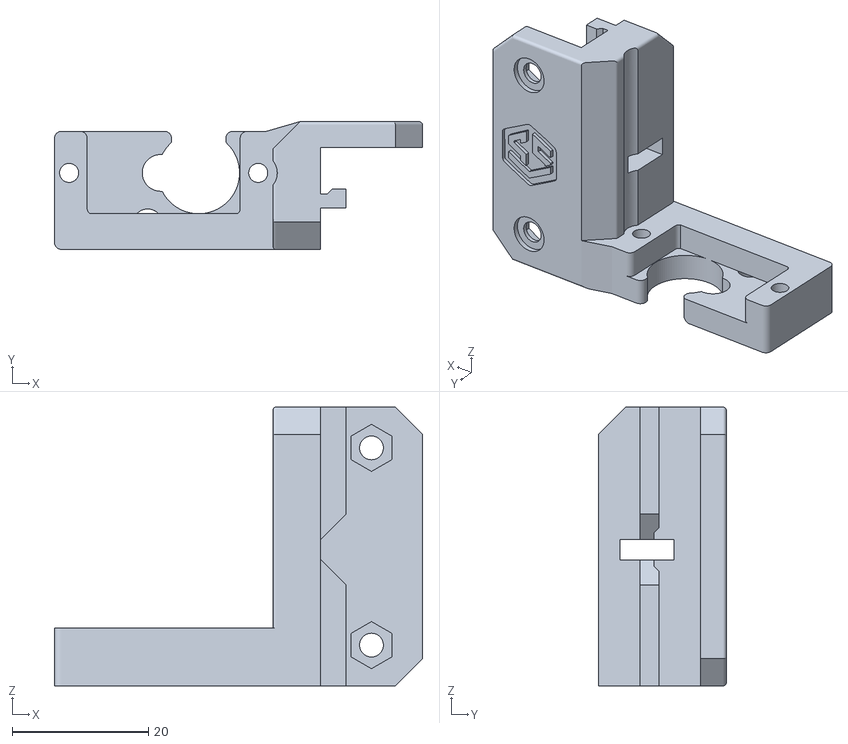
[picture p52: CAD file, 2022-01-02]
STL/RailMountSide.stl
54.1 x 18.8 x 41.0

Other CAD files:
STL/Probe.stl
Experimental/UnklickySlideSwipe(better name pending)/STEP/ProbeTight.step
STL/Arm2.stl
Alternative_Mounts/FrontCowlingMount/STL/SlideSwipe_FrontCowlingMount.stl
Experimental/UnklickySlideSwipe(better name pending)/STL/PlungerSideways.stl
Experimental/UnklickySlideSwipe(better name pending)/STL/ProbeLoose.stl
Experimental/UnklickySlideSwipe(better name pending)/STL/ProbeTight.stl

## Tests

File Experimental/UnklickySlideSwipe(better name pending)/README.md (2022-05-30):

# UnklickySlideswipe (If you have a better idea for a name, let me know)
## Introduction
This is a bit of a mixture of [unklicky](https://github.com/majarspeed/Unklicky/tree/main/Unklicky) and [mechabl](https://www.thingiverse.com/thing:4736440) in a SlideswipeProbe formfactor. There is also a euclid compatible derivative of this called [Unclid](https://github.com/Minsekt/unclid)(I love that name).

### Principle
Basically, the magnet in the plunger bridges the screws on both sides.
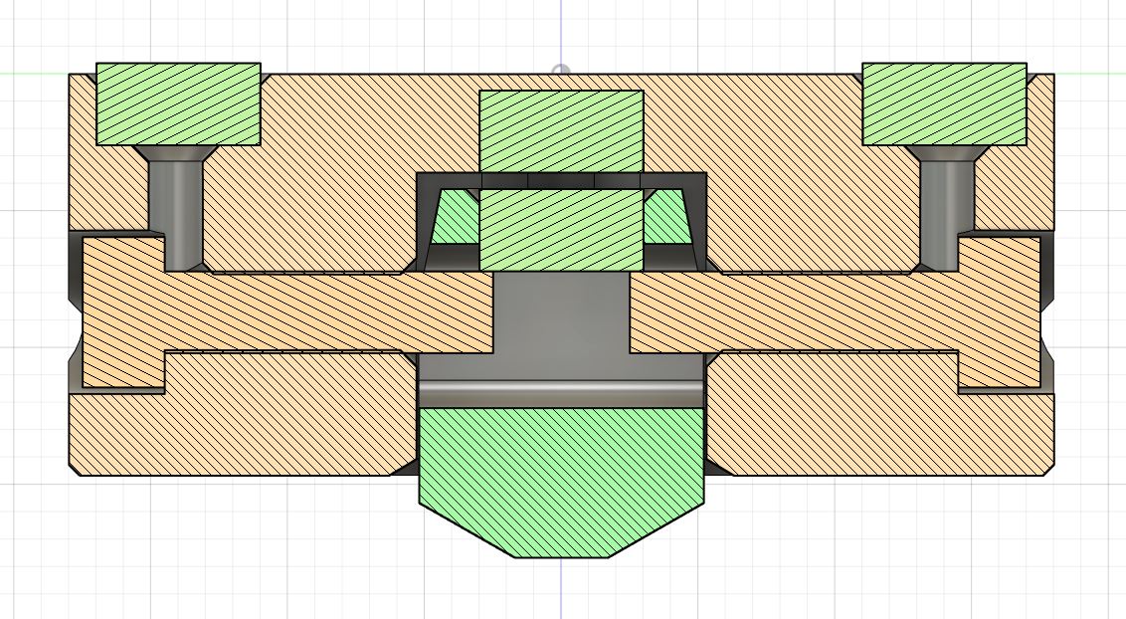
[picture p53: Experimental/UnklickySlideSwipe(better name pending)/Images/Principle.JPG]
Principle


## Pros and cons compared to microswitch version
| Pro | Con |
| ---- | ---- |
| + Much better repeatability | - More sensitive to print quality and assembly |
| + More tolerant to abuse | - Can get stuck open, which is still safe but annoying (this is usually caused by assembly or print errors and amplified by weaker magnets) |
| + Fully symetric |  |
| + Can be made from stuff you probably allready have  |  |
| + Actuation force can be tuned by using stronger or weaker magnets or increasing the distance between them  |  |
| + Larger plunger tip for better repeatability on textured surfaces  |  |

## BOM
- 2x M3x12 Socket Head Screws (Preferably stainless but slightly magnetic)
- 4x 6x3 Round magnets
- 5cm of stranded wire

### Tools
- Some epoxy or superglue (glue is optional)
- A multimeter

## Printing
Ironing for the top and using a smooth print surface is recommended for the plunger.

The loose probe should ideally need no post processing while the tight one need some sanding on the plunger but should perform slightly better.

## Post processing
Remove the integrated support from the plunger.

Make sure there are no blobs on or in the plunger or inside the hole in the probe.

If you printed the tight probe, sand the sides of the plunger until it slides in and out with little resistance.

## Build
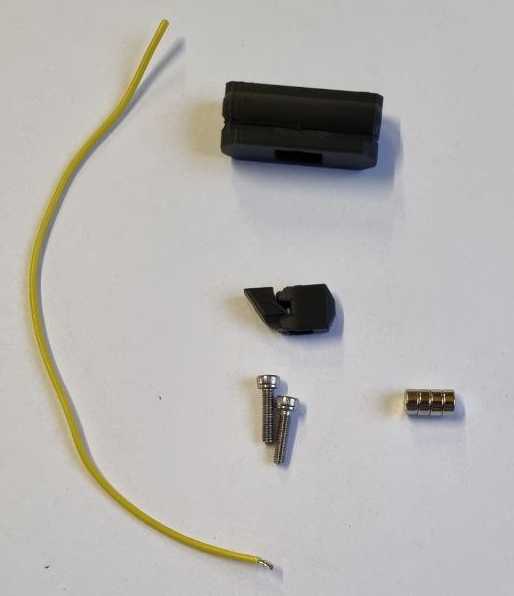
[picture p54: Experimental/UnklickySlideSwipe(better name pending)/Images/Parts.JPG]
Parts

### Magnet spring
Push the probe magnet in the hole (I use the pointy side of the plunger for that, but there are lots of way to do it). The magnet should preferably have the opposite polarity to the docking magnets though same works too.

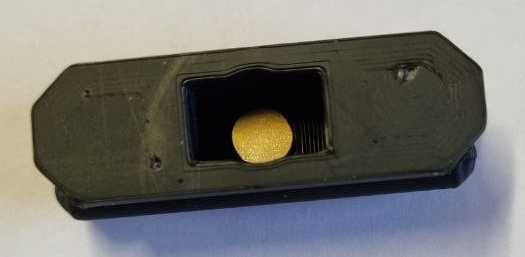
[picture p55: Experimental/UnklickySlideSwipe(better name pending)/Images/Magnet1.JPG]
Magnet1

### Plunger
Press the magnet into the plunger, so it sticks to the top of the probe like shown below.
Make sure the probe still moves in and out of the body easily (though with the resistance of the magnet spring).

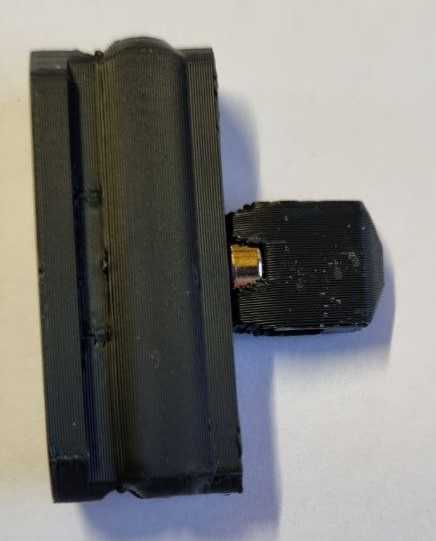
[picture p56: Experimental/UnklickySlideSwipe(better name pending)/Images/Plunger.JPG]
Plunger

### Screws
Strip a couple of cm of the stranded wire.

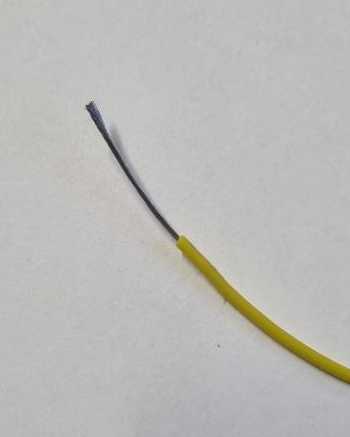
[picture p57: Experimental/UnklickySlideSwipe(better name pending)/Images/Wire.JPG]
Wire


Insert the wire into the top of the magnet hole and push it in to the screw hole a little bit.

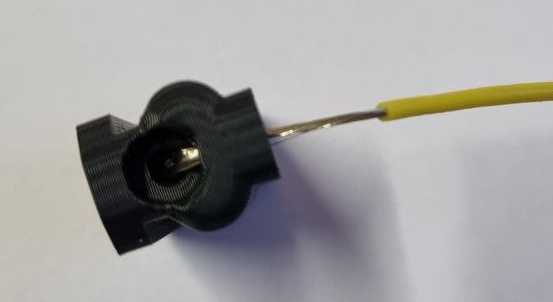
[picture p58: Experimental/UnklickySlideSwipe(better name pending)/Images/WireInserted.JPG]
WireInserted


Screw the screw into the hole (not all the way jet so we can insert the plunger later)

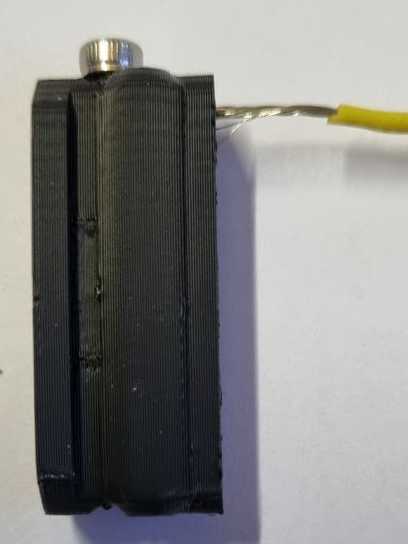
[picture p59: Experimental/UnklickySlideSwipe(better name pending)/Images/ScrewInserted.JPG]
ScrewInserted


Trim the wire so, it stands out about 1 or 2mm from the hole.

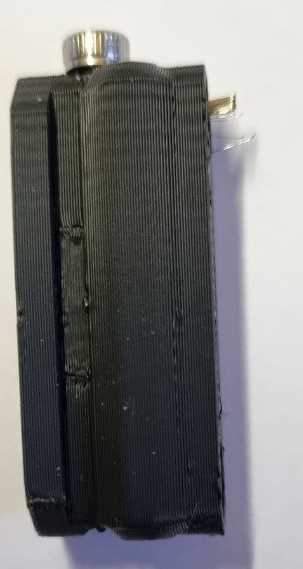
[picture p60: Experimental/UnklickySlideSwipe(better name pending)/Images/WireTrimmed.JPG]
WireTrimmed


Repeat for the other side.
### Dock Magnets
Spread out the wire strands in the magnet holes.

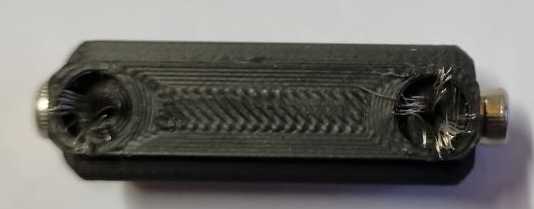
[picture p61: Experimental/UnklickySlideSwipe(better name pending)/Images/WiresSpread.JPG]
WiresSpred


Press the magnets into the holes in the right polarity to fit the mount. A vise can help a lot here, but you can also just push it against a flat surface.

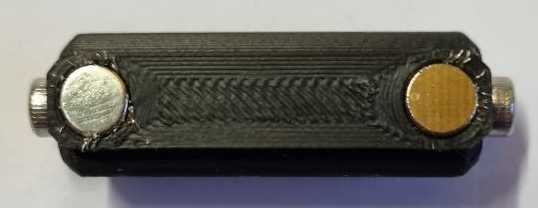
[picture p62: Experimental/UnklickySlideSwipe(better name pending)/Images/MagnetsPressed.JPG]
MagnetsPressed


Trim of the excess wires if they get in the way and measure continuity between the magnets and the screws.

MeasureMagnets

### Lubricate (Optional)
If you have some non-sticky, non-conductive and non-drippy lubricant (like dry PTFE spray) drown the probe and the plunger in it and let it dry.

### Plunger install
Put the plunger into the hole, press it all the way down and screw both screws in all the way. measure continuity between both magnets, without anything touching the plunger it should be connected but break when pushing the plunger in.

Probe

## Klipper setup
All you need to do is recalibrate your z-offset.
I do reccomend working in the probe a bit by running a couple hundred probes through it first (PROBE_ACCURACY SAMPLES=100) as it needs a bit of a work in period before it starts working really well.

## Feedback
Let me know how it worked out for you, you can find me on the voron discord.

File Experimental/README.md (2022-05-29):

This is where I put experimental stuff that is working well enough to be released, there may be less documentation and polish here.

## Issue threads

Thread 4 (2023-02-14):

Suggestion for improving UnklickySlideswipe accuracy due to bed flex on V0

vkvam, 2023-02-14:
Hey! UnklickySlideswipe seems to have a really cool design, thanks for publishing it on Github!

I can't really see a lot of room for improvement on the probe itself, but I think it's possible to adapt it better to the infamous V0 bed flex.

I've been printing some really tiny parts with 0.2 mm nozzle and 0.1 mm layer height on my Voron 0.2 with Kirigami bed, and when applying a mesh I've noticed that the nozzle is closer to the bed the further away from the z rails it is.

Further more, if i get the probe to trigger on the front of the bed, I can actually see the bed flexing ever so slightly.

If I remove the centre magnet intended to push the plunger on to the screws from the probe, and align the plunger magnet so that the two attachment magnets pushes on it– the force required to push it is reduced drastically.

vkvam, 2023-02-14:
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

chestwood96, 2023-02-14:
There is a lot of playing room with the magnet strengths though there are
some tradeoffs, weaker magnets have had the effect you are describing on my
testing too but at the cost of causing false positives a lot more often. I
ended up just using kirigami to mitigate this issue.

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

vkvam, 2023-02-14:
Yeah, I‘m also using kirigami and tested a bit more, there is still is a 0.05-0.1mm diff between front and back of the bed when I run mesh. There must be another issue, unrelated to the probe, since it is so significant and it’s not a big topic among klicky/v0 users.

I’m thinking the pros of the suggestion may apply specifically to whatever issue I’m having, and that the cons outweighs them for anyone else, so I’ll close the issue.

Closed 2023-02-15.

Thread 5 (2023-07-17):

missing SS_STOW_PROBE?

ronsmits, 2023-07-17:
Hi when looking at the code for klipper, I seem to be missing the storing of the probe after the G28 Z. There is 1 after the bed leveling, but not after the homing itself?

chestwood96, 2023-07-17:
Why would you need one there?

Unless I am missing something there all that would cause would be an unnessecary stow and attach between homing z and probing.

Closed 2023-07-21.

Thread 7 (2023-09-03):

Led compatibility

Otann, 2023-09-03:
I have a quick question, is this mod compatible with leds, which are mounted to the bottom of the Y extrusion?

[Like this one](https://github.com/VoronDesign/VoronUsers/tree/master/printer_mods/Jon/1515_led_mount)

chestwood96, 2023-09-03:
Good question, depends on how far down the leds go and it would definitely
interfere with the stock wire routing.

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

Otann, 2023-10-10:
I found that the answer is no, so I've designed [my own mount for led strips](https://www.printables.com/model/599080-voron-02-top-mounted-led) :)
All because I wanded the SlideSwipe so much.

Thank you for the amazing work! 🙌

Closed 2023-09-12.

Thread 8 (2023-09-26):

V0.2 compatible mini AB cowling?

ulope, 2023-09-26:
Do you have any plans to add a replacement cowling that fits the v0.2 Mini After Burner with the swappable hotend mounts?

Also thanks for making this cool mod!

ulope, 2023-10-05:
Thanks, in the meantime I found a ready-made mod on Printables: https://www.printables.com/model/576996-voron-02-r1-slideswipe-mod

chestwood96, 2023-10-05:
Nice good to know, let me know how that works for you.

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

Closed 2023-10-05.

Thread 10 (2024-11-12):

Images for microswitch installation in probe do not match description

swobbee-dev, 2024-11-12:
Hi,

the documentation states:

"After the glue has dried insert the microswitch _so the plunger is in the middle of the probe_."

However, in the pictures below the microswitch is installed exactly the other way around.

Unfortunately I noticed this too late, and since my switch had a bit of wiggle room side to side I had glued it in place...

chestwood96, 2024-11-12:
That does indeed look the wrong way around on the picture but you are not
supposed to glue the switch. Being able to replace/rotate the switch easily
is a feature here.

You may also want to take a look at unklicky slideswipe, it is pretty much
universally better if you can build it right.

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

swobbee-dev, 2024-11-12:
Oh, interesting! Is this a drop-in replacement for the klicky probe? Will this work with the 5mm magnets on the toolhead?

Btw, I love the mechanism you built here. Its so satisfying to watch :)

chestwood96, 2024-11-12:
Drop in, but uses the same 6mm magnets as everything else, no 5mm ones
anywhere

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

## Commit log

2022-01-06 typo in wiring url
2022-01-06 fixed stl orientation
2022-01-11 Fixed confusing filenames
    [Cowling_Dragon_SlideSwipe.step]
2022-01-18 Added front mount
    [SlideSwipe_FrontCowlingMount.step, SlideSwipe_FrontCowlingMount.stl]
2022-01-18 Messed up folder structure
    [SlideSwipe_FrontCowlingMount.step, SlideSwipe_FrontCowlingMount.stl]
2022-03-03 added KlickyAdapter
    [SlideSwipe_KlickyAdapter.step, Slideswipe_KlickyAdapter_mount.stl, Slideswipe_KlickyAdapter_probe.stl]
2022-05-29 Added UnklickySlideswipe
    [PlungerSideways.step, PlungerSideways.stl, ProbeLoose.step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]
2022-06-03 replace individual step files with full assembly step
    [Arm1.step, Arm2.step, Probe.step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]
2022-06-04 update assembly cad
    [SlideSwipe_Assembly.step]
